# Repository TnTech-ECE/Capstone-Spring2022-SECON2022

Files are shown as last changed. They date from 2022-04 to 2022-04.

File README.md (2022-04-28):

# SECON2022
## Tennessee Tech SoutheastCon 2022 Robot Project
## Executive Summary
The goal of this project was to design and build an autonomous robot to compete in the 2022 IEEE SoutheastCon Student Hardware Competition. 
The theme of the competition was Mardi Gras, and the competition format reflected this. The robot had to navigate a track while completing 
tasks and avoiding obstacles, all within a three-minute time limit. The team consists of two Electrical Engineers and two Computer Engineers. 
The engineers on this team leveraged their academic background in microcontrollers, power, and control systems, and acquired other necessary 
knowledge in areas such as computer vision and Mechanical Engineering. 

## Version Contained In This Repo
The version of the project contained in this repo has been updated since the competition. All software files necessary to play the full game 
are contained under the Software heading.

## Outcomes
Due to last minute optimizations before the competition, the team was unable to showcase the full design and capabilities of the robot. 
This project earned a ranking of 7th place out of the 38 teams that attended the competition. The initial proposed budget for this project 
was $2000, and the final BOM indicated a final budget of $2,023.49.

## Video

<figure class="video_container">
  <iframe src="https://youtu.be/yNQZh_yY1AQ"> </iframe>
</figure>

## Pictures
### Front of Robot

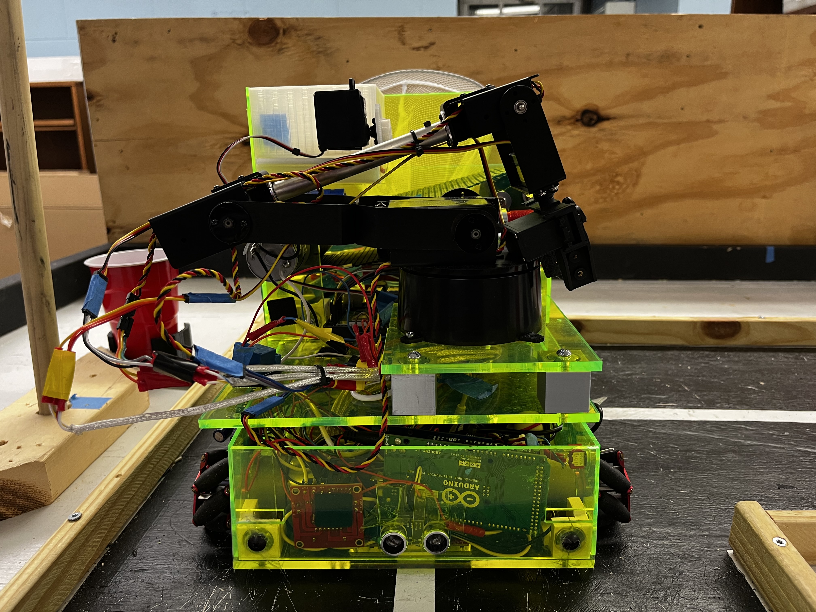
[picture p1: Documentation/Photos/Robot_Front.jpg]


### Right Side of Robot

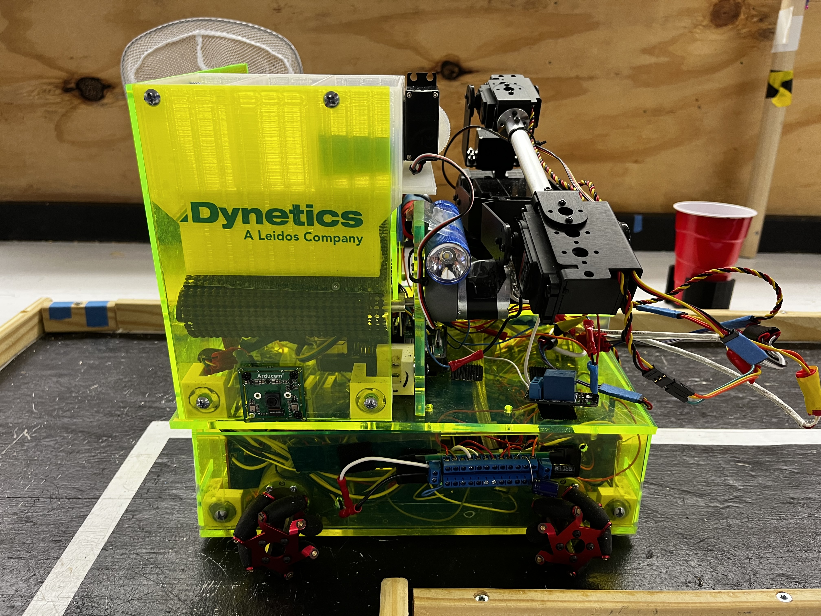
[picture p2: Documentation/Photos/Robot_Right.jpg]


### Left Side of Robot

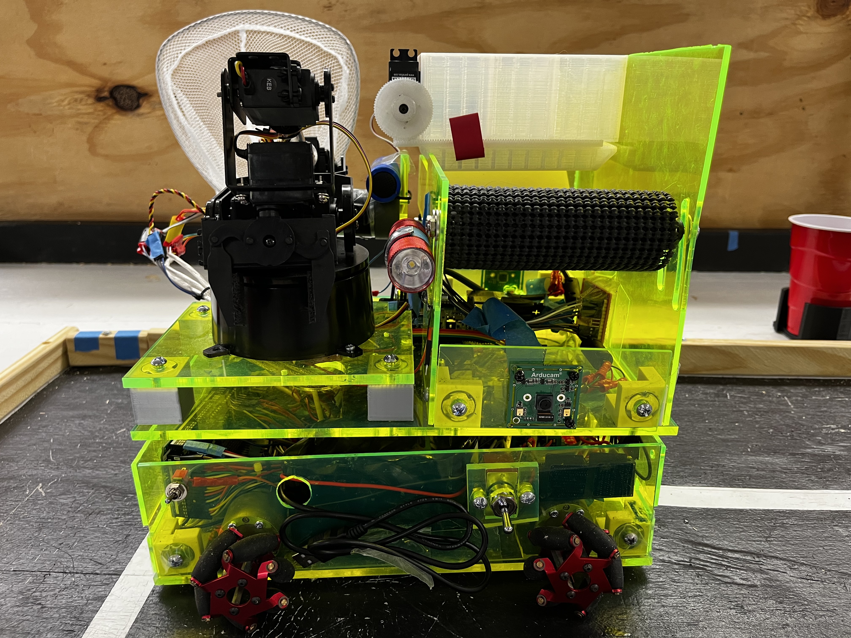
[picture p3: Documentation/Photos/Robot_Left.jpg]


### Back of Robot

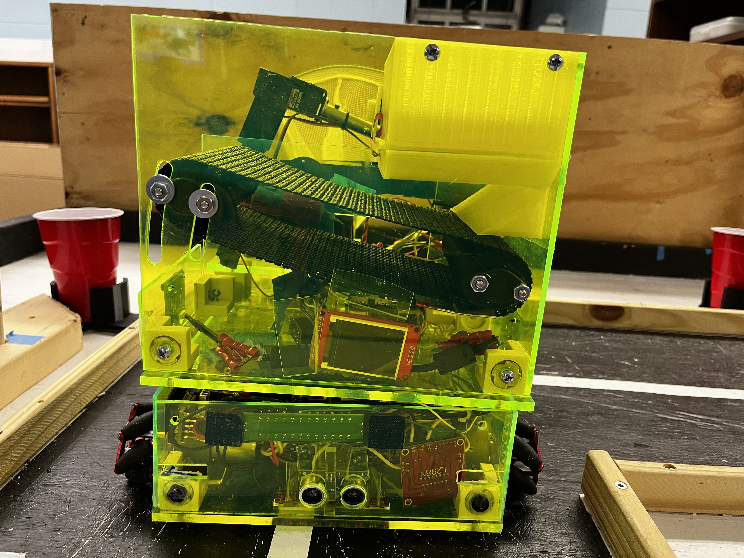
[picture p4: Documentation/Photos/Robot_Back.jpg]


### Top View of Robot

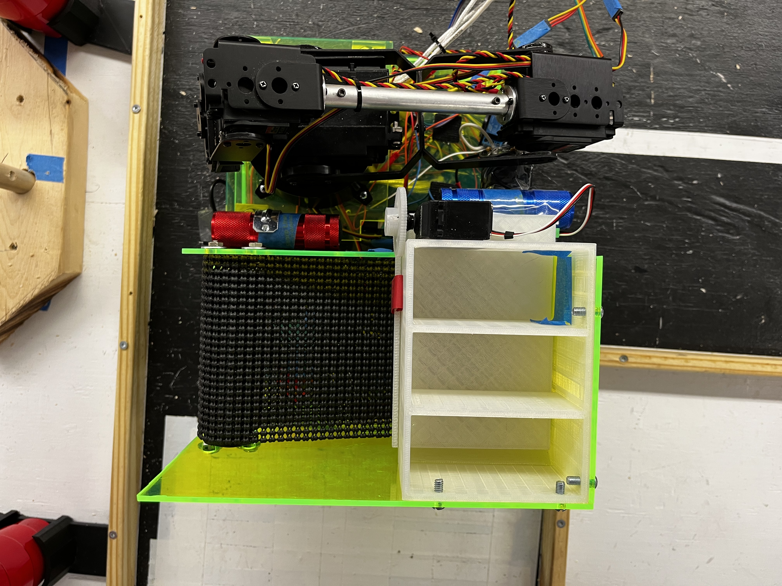
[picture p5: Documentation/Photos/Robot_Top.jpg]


### Interior of Lower Chassis

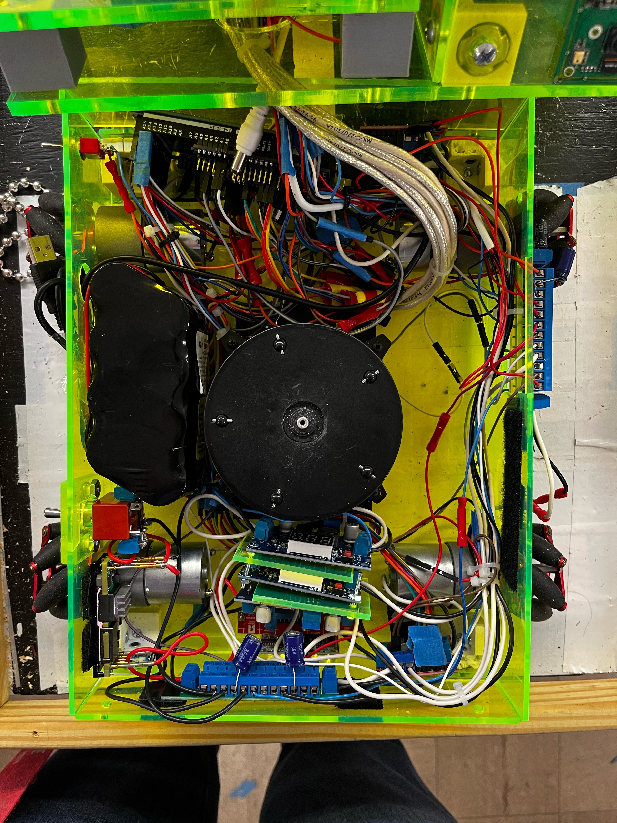
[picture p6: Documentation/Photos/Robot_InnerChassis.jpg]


## About Us
As mentioned in the summary, this team consisted of two Electrical Engineers and two Computer Engineers. The two Electrical Engineers are 
Chase Garner and Sawyer Hall, and the two Computer Engineers are Daniel Summers and Lexi Sheeler. The faculty member that oversaw the 
development of this project is Jesse Roberts. There was no customer for this project, however the project was designed to meet the 
specifications provided by the competition organizers.

## Repo Index
### Project Documentation
<ul>
  <li>Design Documents
    <ul>
      <li>3D Models</li>
      <li>Power</li>
    </ul>
  </li>
  <li>Bill of Materials</li>
  <li>Datasheet</li>
  <li>Project Poster</li>
  <li>Photos</li>
</ul>

### Reports
<ul>
  <li>Project Proposal</li>
  <li>Design Phase 1</li>
  <li>Design Phase 2</li>
  <li>Final Report</li>
</ul>

### Software
<ul>
  <li>Raspberry Pi</li>
  <li>SECON_Arduino</li>
</ul>

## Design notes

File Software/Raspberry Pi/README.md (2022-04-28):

## File(s): 				
detect_shapes.py, shapedetector.py, colorlabeler.py, shapeLength.py

## Author(s): 				
Daniel Summers, Lexi Sheeler

## Target Hardware: 		
Raspberry Pi 4 (4 GB) Running Ubuntu 21.10

## Purpose: 				
 This software is responsible for the Vision System of Tennessee Tech's SoutheastCon 2022 Robot. This software will detect the presence
						of nets on the game board and communicate this to an Arduino MEGA 2560 over serial communication. Additionally, this software will output
						an image to a TFT Screen. This serves as a method of achieving points as well as indicating that the Pi is running correctly.

## Software Dependencies:	
Python 3 (Necessary Libraries: imutils, cv2, serial, digitalio, board, PIL, adafruit_rgb_display), the file Tech.bmp (this is the bitmap
						image to be displayed on the TFT screen)

## External Connections:	
This software is designed to be ran in conjunction with an Arduino MEGA 2560 (see SECON2022/Software/SECON_Arduino for software) via UART.
						Reference SECON2022/Documentation/DesignDocuments for all external hardware connections. 
						
## Installation:			
Download and Install Python3 and its necessary libraries to the Raspberry Pi using apt and PIP (each where necessary)

## Running/Use:			
These files are designed to be ran with sudo priviledges automatically on boot up. To accomplish this, the default user of the Pi must be 
						given the necessary sudo priviledges, and the console command 'sudo python3 detect_shapes.py' must be added to the list of commands to be ran
						on startup. The team implemented this by adding the command to the default user's .profile script (Note: for this workaround, requiring the 
						default user's password when executing sudo commands must be disabled. This is a security risk that should not be implemented if the Pi is to
						be used for other applications.)

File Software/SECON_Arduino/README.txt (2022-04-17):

File: 					SECON_Arduino

Author(s): 				Chase Garner, Sawyer Hall, Daniel Summers

Target Hardware: 		Arduino MEGA 2560 with Adafruit Servo Shield

Purpose: 				This software is responsible for the motor control and sensor readings for Tennessee Tech's SoutheastCon 2022 Robot. 
						This serves as the main gameplay control for the robot.

Software Dependencies:	Ardunio IDE

External Connections:	This software is designed to be ran in conjunction with a Raspberry Pi (see SECON2022/Software/RaspberryPi for software) via UART.
						Reference SECON2022/Documentation/DesignDocuments for all external hardware connections. 
						
Installation:			Connect the Arduino MEGA 2560 to a computer via USB. Using the Arduino IDE, flash the given code to the Ardunio.

Running/Use:			After installation, the code will automatically begin running when the Arduino is powered on. Immediately after powering on, the 
						robot will begin calibrating. At this time, the line following sensors (See SECON2022/Documentation/) should be calibrated by providing
						them with a reference for both black and white (This implementation expects a white line with a black background). After calibrating,
						the arduino will entire a standby loop until the start switch is flipped (the GPIO input pin connected to the start switch will have its
						pull up resistor enabled, driving its signal high. Connecting the other side of the switch to Ground will pull the GPIO pin down when the 
						switch is flipped, starting the gameplay routine. Any input of 0/Ground on this pin will achieve the same result. Power Cycling the robot 
						is required to restart the routine.

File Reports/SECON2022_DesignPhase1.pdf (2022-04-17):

# Design Phase One

Chase Garner, Sawyer Hall, Lexi Sheeler, Daniel Summers
Electrical and Computer Engineering Department Tennessee Technological University Cookeville, TN
ncgarner42@tntech.edu, sjhall43@tntech.edu, aasheeler42@tntech.edu, dbsummers42@tntech.edu
I. INTRODUCTION
A. Problem Definition

The South Eastern Conference (SECon) is a yearly IEEE event comprised of several competitions. One such competition is the hardware competition, where students from many schools across the region design and build a robot to compete in a unique challenge. Because the conference is being held in Mobile, Alabama, the competition is Mardi Gras themed to reflect the history and origin of the festival. This year’s hardware competition requires the robot to navigate an L-shaped street within a three-minute time limit. In addition to navigation, the robot can complete challenges to earn points. The tasks include: removing beads from a “tree”, placing the beads in “trash bins” or shooting them into fishnets, and moving a marshmallow off the roadway into gaps in a barricade.
There are several rules and specifications that the design must adhere to. The first and potentially most important constraint to meet is that the robot requires complete autonomy. To meet this constraint, the robot must be capable of decisionmaking to identify randomly placed obstacles and challenges. In addition, the robot must be contained within one cubic foot at the start of the competition, but may expand beyond this specification after the run has started. It is also specified that the robot may not break apart and must remain one unit for the entirety of the run. Finally, the robot may not cause damage to the track or harm bystanders. Any violation of these constraints will result in immediate disqualification at the judges’ discretion.
B. Conceptual Design

At the beginning of the design process, key competition rules and point gaining tasks were identified. The point breakdown played into the first design phase in several ways. The scoring scheme was broken down and the maximum number of achievable points was determined. This allowed for selecting which way the robot could earn maximal points without the need to complete every task outlined in the guidelines. This led to a design that is targeted towards shooting beads into the nets instead of trying to place them into the cups along the sidewalk area. Along with this decision, the team also elected to not place high importance on removing the marshmallow from the track because it is only a one-point deduction if left on the track. No attainable designs were identified by the team, and focus was instead placed on areas which are integral to being competitive, such as the navigation system and drive train.
The robot is broken down into seven systems: main controller, power, navigation, drive train, appendages, shooting mechanism, and peripherals. Each system is then broken down further into atomic subsystems. There will be three microcontrollers: the main controller, a navigation controller, and a peripheral controller. Serial communication will be used between the main and navigation controllers, and the peripheral controller will only require power to operate. The main controller is responsible for interconnects between systems, excluding power, which will directly connect with all systems. For the next phase of the design process, component specifications will be defined first at an atomic level, then working up until the whole system has been defined.
C. Broader Impacts

Beyond the competition itself, this project aims to serve as a way to demonstrate the quality of both the Tennessee Tech Electrical and Computer Engineering (ECE) Department and the Tennessee Tech IEEE. The Tennessee Tech IEEE chapter has a longstanding tradition of fielding competitive, winning teams at SECon, and this project serves to continue such a tradition. Additionally, due to the current pandemic, interest and involvement in the IEEE chapter has massively decreased over the last two years. This project will generate more interest in IEEE from ECE students while also providing IEEE members with hands-on experience with robotics and programming. Because of the involvement of the IEEE chapter, the design of the peripheral system was changed to use its own microcontroller and an analog circuit to control the LEDs. This allows the IEEE members to work on these systems independently of the robot’s development, and it ensures they receive experience in elements of both electrical and computer engineering by incorporating both analog and digital circuitry and programming.

D. Larger Process

The Design Phase I document is written with the intent of removing ambiguity and presenting a more clearly defined system. The document should leave the reader with a clearer understanding of how the competition has led the team to make the design choices presented in the following sections.

In addition, ideas presented in this document will be further built upon in future design phases.

II. CHASSIS

The robot’s chassis will be divided into a lower section, which will house the majority of the electronics, and an upper section, which will serve as a platform for the robotic arm and shooting mechanism. The chassis and all external systems must conform to the 1 cubic foot constraint set by the competition. Because of its size and simple structure, it is intended for the chassis to be constructed with acrylic sheets instead of 3D printing it, but additional material options are still being considered. The main justification for this decision is the team’s desire to avoid possible 3D printer errors that are likely to occur during the longer print times that would be necessary for the larger aspects of the chassis. In order to verify that the chassis conforms to the 1 cubic foot limit while still maintaining enough volume to house the robot’s internal components, the chassis will need to be a somewhat detailed 3D model. Additionally, the size of the robot should be minimized in order to allow for a smaller turning radius. The lower chassis (Figure 1) will be a stationary platform in order to minimize the amount of turning required. With a 1 square foot footprint, the robot would be over 16 inches diagonally. This could prevent the robot from turning within the 16-inch width of the track. Instead, the lower chassis will only be required to turn during the two 90 degree turns in the track, where the effective width is much wider. The lower chassis will contain the drivetrain, navigation sensors, each of the microcontrollers, and the power supply circuitry, including the battery. The main purpose of the lower chassis will be to house these components, but it will also be responsible for collecting the marshmallow obstacle from the track. It is the intention of the team that collecting and pushing the marshmallow will be handled by a passive system that will be incorporated in the chassis’ shape and design, but the exact specifications of such a passive system must still be determined. The main constraint of the lower chassis will be the size limitation of the competition. The chassis, including the wheels on each side and the passive marshmallow system on the front, must all fit within the 1 square foot footprint of the robot.
Instead of requiring the entire robot to turn and face each target, the upper half of the chassis will be constructed in such a way that it will freely rotate at least 180 degrees to allow for the shooting mechanism to “aim” in each direction. However, the rotation must not interfere with the wiring connections between the lower and upper chassis. This turntable will house the robotic arm and the shooting apparatus. Additionally, the upper chassis (Figure 3) will serve as a storage mechanism for the beads between being collected and being shot into the nets (Figure 2). Upon being placed into the storage mechanism, the beads must be sorted into three separate containers to be individually loaded into the shooting apparatus. The number of containers was chosen in order to comply with the competition rules stating that additional points would be awarded for each

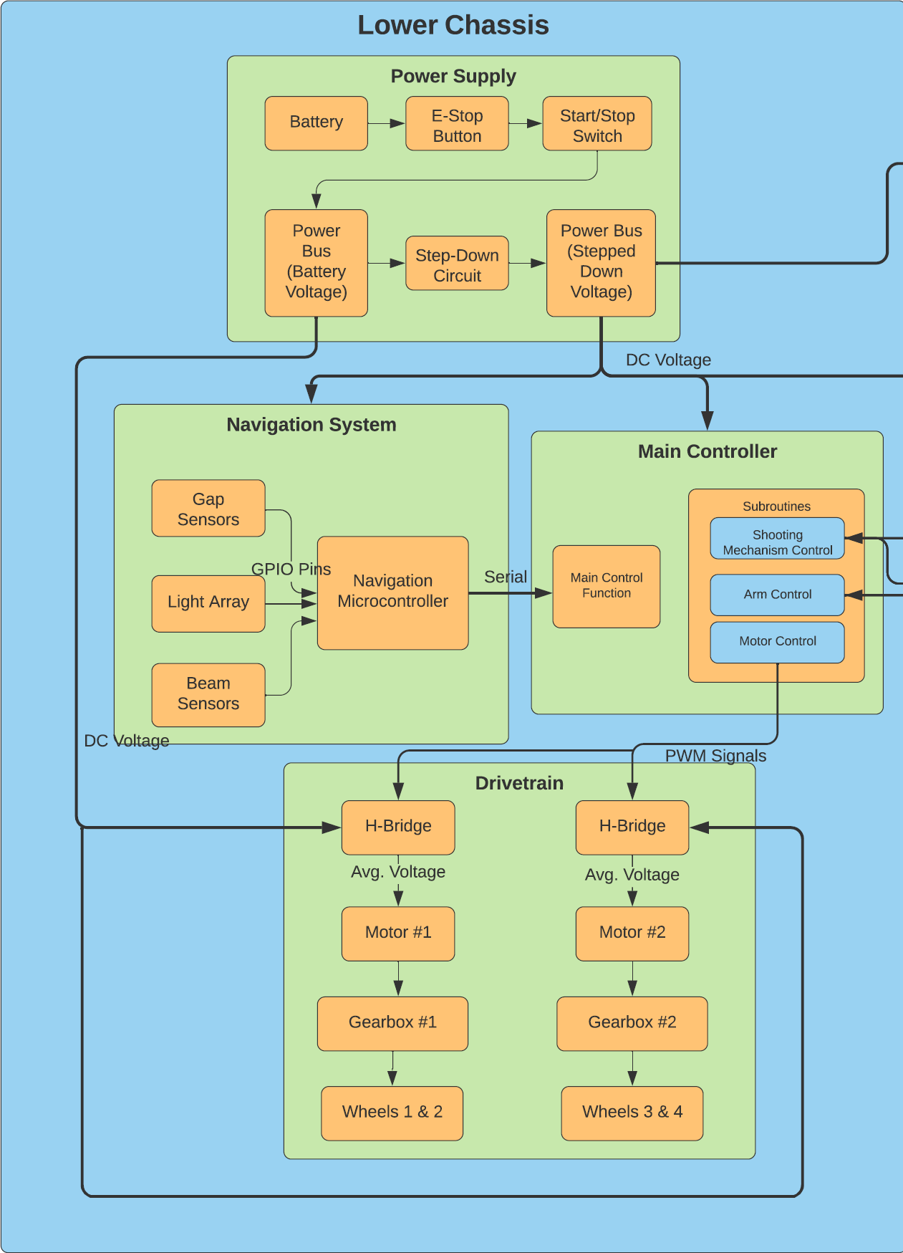
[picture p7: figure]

Fig. 1. Lower chassis block diagram

net containing at least one bead. Because there are three nets, three was chosen for the number of containers. These containers will be bottomless, but the housing of the shooting mechanism will serve as a temporary bottom. To “reload”, the containers will be moved over an opening in the housing, allowing the beads to fall onto the belt. However, this method must be tested to ensure that the beads consistently do not get stuck in the sorting mechanism. In order to test the most optimal sorting configuration, a physical mock-up of the system must be constructed. The dimensions of the divider will then be experimentally varied and the percentage of beads in each container, as well as the percentage of beads that get stuck, will be measured. The configuration that yields the most balanced percentage of sorted beads and the lowest percentage of stuck beads will be chosen for the final design.

III. CENTRAL CONTROLLER
The central controller (Figure 4) of the robot will consist of a single Arduino Mega 2560 microcontroller. This specific hardware component was chosen for its robust functionality, simple programmability via Arduino’s predefined libraries, and large number (54) of General-Purpose Input-Output (GPIO) pins, of which 15 can be used to generate Pulse Width

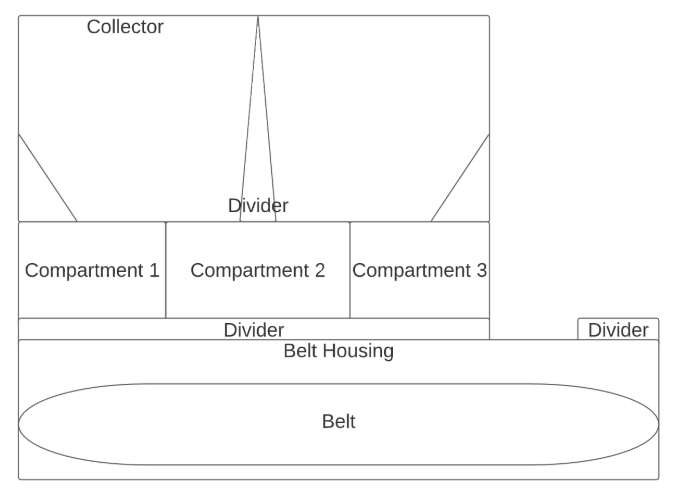
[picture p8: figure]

Fig. 2. Loading mechanism

Modulation (PWM) signals. The microprocessor operates at 5 Volts and is recommended to be powered by 7-12 volts which will be provided by the step-down circuitry of the robot’s power supply [1]. Additionally, a serial connection must be established between the central controller and the navigation system. This serial connection will relay commands from the navigation system’s microcontroller to the central controller, where they will be interpreted in order to determine the proper control subroutines to be run. This interpretation and serial communication will be handled by the central controller’s main control function, which will then trigger a number of separate subroutines that are responsible for the central controller’s outbound communication to the motors, arm, and shooting mechanism.
The motor subroutines will communicate with the drivetrain’s motor drivers via its GPIO pins to achieve the desired speed and direction of each of the two motors. This functionality will include both starting and stopping the motion of the robot, navigating the 90 degree turns in each direction, and propelling the robot both forward and backwards along the track. The arm subroutines will function by using inverse kinematics to provide the necessary positional information to each of the arm’s servo motors to achieve the desired endpoint position of the arm. Such routines will include picking the beads from each tree and placing the beads in the chassis’ storage container. This information will be provided to each individual servo via dedicated GPIO pins. Lastly, the subroutines related to the shooting mechanism will be responsible for rotating the upper platform of the chassis to “aim” the mechanism in the correct direction, providing a signal to the shooting belt’s motor, and ”reloading” the mechanism by shifting the storage container to allow for the next set of beads to fall onto the belt. Each of these motor control subroutines will drive separate PWM pins of the central controller. Consequently, each of these subroutines will accept additional feedback inputs from these external systems. This feedback will be used to align the subroutine’s expected

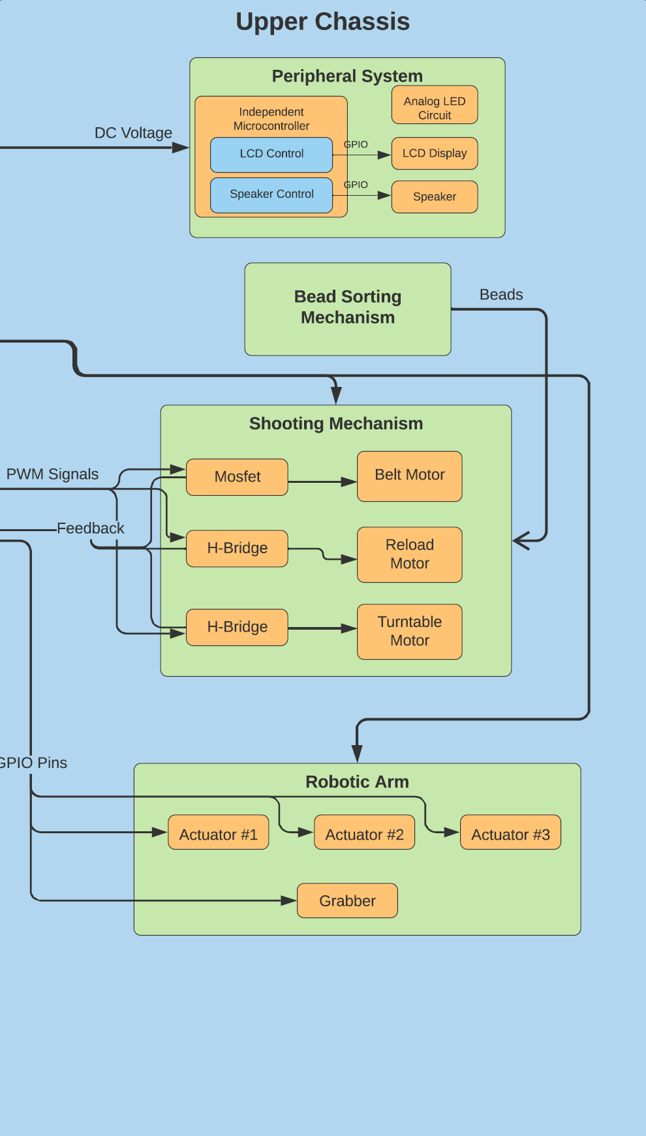
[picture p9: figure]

Fig. 3. Upper chassis block diagram

behavior with the actual behavior of the mechanical parts and will be provided via additional GPIO pins.
Because of the software-based nature of the central controller, the elements of the programming language can be assumed to behave in the way they are defined by the language. However, the software’s behavior must be closely emulated when simulating and testing the various components driven by the software. Without closely representing the software during this testing, the components under test can not be guaranteed to behave in the same manner when they are controlled by the software. In addition, extensive experimental testing will be required to adjust the software to meet specific needs of the robot. For instance, timing tests must be conducted to ensure that enough time has passed for all of the beads to be launched by the shooting mechanism before the motors are turned off.

Lastly, the datasheet of the Arduino must be thoroughly read and understood to ensure that the microcontroller is capable of producing the output voltages and currents required by the component hardware.

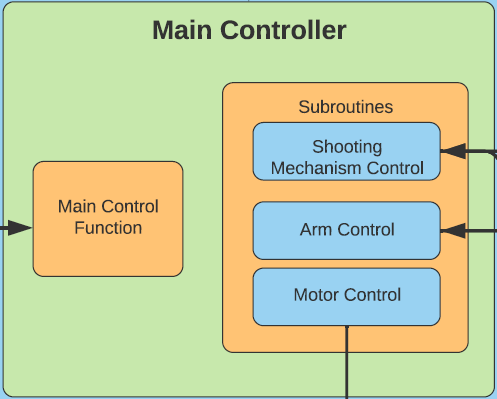
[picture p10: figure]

Fig. 4. Central controller block diagram

IV. POWER

The battery voltage will be determined by what is needed to power the DC motors. Because of competition specifications, the robot is required to have a visible and easily accessible emergency-stop. To ensure no damage to components, the emergency stop is intended to stop only moving parts of the robot. Therefore, the emergency-stop will be the interim between the battery and motors. The emergency stop will be utilized to stop the robot in case of a major malfunction. Like the emergency stop, the competition specifications require the robot to have a clear start/stop switch. The start/stop switch will then be connected from the emergency stop to the power bus. The power bus will distribute the primary voltage to the step-down circuit and the H-bridge. The H-bridge will then connect the needed voltage to the DC motors. The step-down circuit will then decrease the battery voltage to the needed voltages for the rest of the components. The step-down circuit will be purchased and not built by the team. The step-down circuit will then be connected to two separate power buses. The peripherals will be connected to one power bus, while the navigation sensors and main controller will be connected to the other. The power circuit will need to be tested through the utilization of LTSpice. The team will test the step-down circuit and will then know that the systems work correctly by finding the output voltage and current at the step-down circuit.

V. NAVIGATION

The navigation system (Figure 6) is responsible for identifying objects and making decisions based on inputs from a light array, beam sensors, and gap sensors. These decisions will

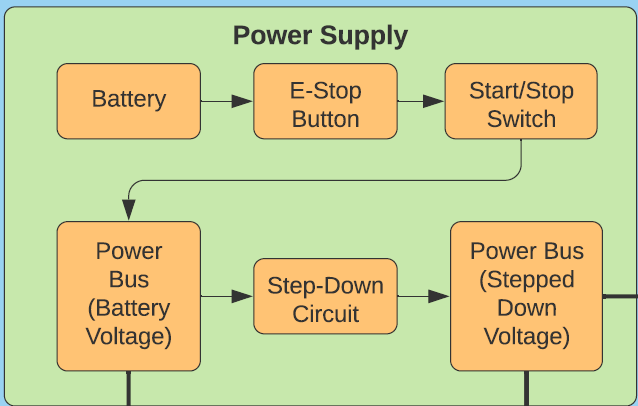
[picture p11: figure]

Fig. 5. Power system block diagram

then be sent to the main microcontroller via serial communication and relayed to the necessary systems. All transmissions between these microcontrollers will include an acknowledge message when the receiving controller accepts the instruction message.
Due to high computational demand and number of available ports, it was decided that the navigation system should include its own microcontroller as to not overwhelm the main controller. The navigation system will require constant monitoring of the sensors, as well as decision making based on the inputs, making this a completely separate system, except for serial communication with the main microcontroller.
The navigation microcontroller will enable interrupts from sensors after the turn around at the end of the track. If the sensor detects specific objects, it will interrupt the drive commands and prompt the correct subroutine. This information will be sent to the main microcontroller in a series of commands: adjust left, adjust right, forward, backward, left turn (90°), right turn (90°), ready to shoot, and arm ready for pick-up/drop. These commands will be appropriately carried out by the main microcontroller and other necessary systems. The light array will be mounted on the underside of the base to assist with track traversal, using the painted white line on the track. The array will allow for small deviation from the painted white line, but will trigger left and right adjustment commands to be sent to the main microcontroller if it strays too much. If the sensor detects a 90° angle in the line, it will send a corresponding command to turn in the correct direction. When it reaches the end of the line, it will send a message to reverse.
The beam sensors will be used to differentiate between power poles and nets based on height. There will be two beam sensors mounted on each side of the chassis, one at approximately 5” and the other pointing up aiming for approximately 18”. When both sensors on one side detect an object, it is identified as a power pole and the robot will continue moving. If only the lower sensor detects an object, the obstacle will be labeled as a net, and a message will be sent from the navigation system to the main microcontroller.

The main microcontroller will follow instructions directing the robot forward or backward until the shooting mechanism is properly lined up. When the mechanism is lined up, the navigation system will then send a ready to shoot command to the main microcontroller to allow the shooting mechanism to fire. After fired, the navigation system will proceed forward and repeat the process until all three nets are identified and beads are fired. At this point, the robot will return to the starting square and end the round.
The gap sensors will also be mounted on the side of the chassis and identify 4” gaps in the barricades. When a gap is identified, the navigation system will alert the main microcontroller which will then trigger the marshmallow subroutine to move the marshmallow off the roadway through the gap. While conceptually these sensors should work, issues may arise further down the line. Options for individual sensors and the overall system are continually being researched to find the best fit. After researching what sensors would be best, the team decided on the beam sensor for identifying nets, but are unsure of what complications may arise in testing relating to the netting material. Because the material is thin and not solid, most sensors will be unable to detect it, which is why discernment is taking place by pole height.
Due to the nature of the system, it will be primarily software, which is difficult to analytically test and measure. As long as used properly, predefined library functions will operate as expected, so the majority of testing will take place on communication between the microcontrollers. For testing purposes, signals sent from the navigation system will be measured and compared to signals received by the main microcontroller.

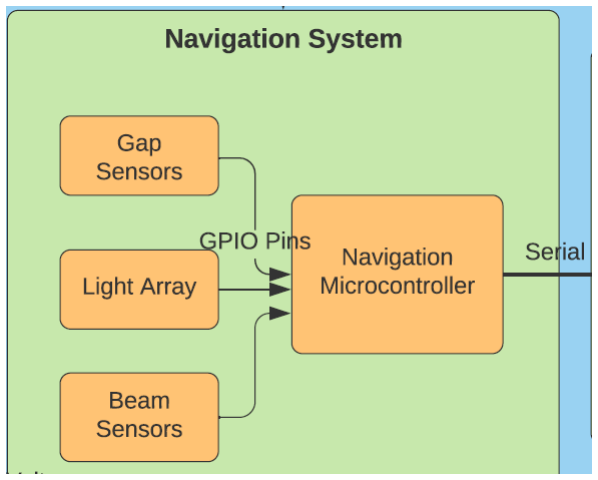
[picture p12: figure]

Fig. 6. Navigation block diagram

VI. DRIVE TRAIN
This year, the environment that the robot will compete in is an L-shaped track. A large portion of the available points in the competition are rewarded solely based on the robot being able to navigate the track back and forth. As such, robot mobility is a critical component of the competition, and vital for the team’s success.
The drivetrain subsystem of the robot (Figure 8) is responsible for moving the robot along the track. “Drivetrain” is an umbrella term that includes all parts that enable the robot to move through space, e.g., motors, wheels, gears, and so on. The drivetrain of this robot will be designed as a differential drive. A differential drive operates on the concept of moving the wheels at different speeds to enable steering. In total, the robot will have two DC motors and four wheels. The pair of wheels on either side of the robot will be connected to their respective motors via a system of gears, belts, or combination of both. One specification that the team will have to keep in mind is the size spec of the robot. The robot will need to be contained within 1 cubic foot which means that the drive train can be at most 1 square foot in area.
Selecting the right motor and understanding its performance characteristics is an important part of designing a drivetrain. A generic graph of DC motor performance is shown in Figure 7.

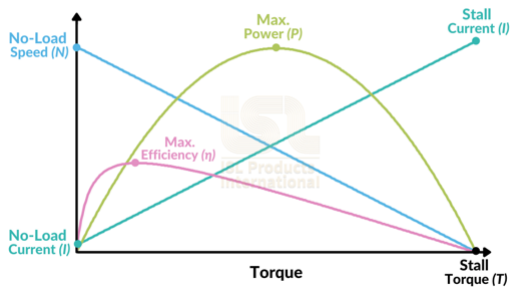
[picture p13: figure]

Fig. 7. Calculations of Arm

As can be seen in the figure, speed and torque of a motor are inversely proportional. As torque increases, speed gradually decreases. In addition, current and torque are directly proportional. At very fast speeds, the motor consumes little current and produces very little torque. This is an issue that can be alleviated with the use of gears. Attaching a gearset to the motor shaft will cause it to run at a lower speed, thus consuming more current and generating more torque. The amount of torque needed in this application is dependent on the weight of the robot and the desired acceleration. Given that the competition environment is a level track, it is not expected that a great amount of torque is needed. Only enough torque is needed such that the robot can accelerate at a reasonable rate and then maintain its velocity. For these reasons, it was decided that two DC motors would suffice. Using only two motors to drive the robot decreases the amount of complexity and needed parts when compared to driving four motors separately. In addition, the team will need to determine how fast the maximum speed of the robot should be when navigating the track, and from there determine the gear ratio necessary to accomplish the task. Gear ratios work to linearly decrease the speed of the motor shaft. For example, a gear ratio of 2:1 means that the shaft will spin twice as slow and generate twice as much torque. Many DC motors come with predetermined gearboxes already attached to the shaft and are referred to as geared motors. Geared motors are a common solution in mobile robotics applications.
As the robot must be completely autonomous, this means that no member of the team will be allowed to do anything to affect the robot’s performance after the run has started. Autonomous operation of the robot will require that the drivetrain system receives commands from the main microcontroller that detail speed and direction for the motors. The method of motor control will have to utilize feedback so that the commanded velocities are not random and reflect where the robot needs to go. One very common method of control is the Proportion, Integral, Derivative (PID) loop. This method of control is common in navigation applications. The proportion coefficient corresponds to how large the error is at any given time, the integral coefficient corresponds to the duration of the error, and the derivative coefficient corresponds to how quickly the error is changing. Using a combination of the three will allow the robot to navigate autonomously while maintaining the desired course.
PID controllers are only effective when they have been properly tuned and utilize the optimal coefficients. Methods of tuning a PID controller vary depending on the system in question. For an autonomous robotic application, a model-based approach may be appropriate. The electrical characteristics of DC motors are well understood, and they can essentially be modeled as a series RL load. This is advantageous for the engineers because a good starting point can be found even without hardware. One software that can be utilized to create a simulation is Simulink. In Simulink, the team would be able to create models of the system and test the responses. Graphs of the response can be created in Simulink that give a visual representation of the system response to error. One thing to consider when viewing these graphs is how much power is required to achieve the response. The amount of power will need to be feasible for our system. Any model-based tuning of the system would of course have to be manually tested by entering the determined PID coefficients into the motor controller and testing the navigation capabilities of the hardware itself. Once the coefficients have been entered into the hardware and the navigation performance has been tested, further tuning will likely be required in order to optimize the performance of the system. This will consist of changing each of the coefficients independently to see how it affects the system. The team will need to have a good understanding of how each coefficient affects the system so that this process relies less on trial and error. It is desirable that the system have a quick yet smooth response to error and that it is able to navigate the entire track while following the white line in the center.

The motor controller will generate Pulse-Width Modulation (PWM) signals to either a dual-motor H-bridge unit or two separate H-bridges that will provide power to the motors. PWM is a method of rapidly opening and closing a switch in a circuit that contains some main power source. The act of opening and closing the switch gives the engineer control over the output voltage to the load. A higher duty cycle (the percentage of the time the switch is closed) will result in a higher average voltage, and vice versa. PWM is advantageous to this project because it will allow the robot to spin wheels on either side of the unit at different speeds, giving the robot the ability to turn and navigate more easily. The team will need to determine a top speed for when the error is zero and the robot is driving directly along the line. All other commanded speeds will be calculated as a percentage of the top speed using the error and PID coefficients. The method of verification for the motor drivers will be LTSpice. An H-bridge is modelled as four transistors, two on each side of the motor. The direction of the current through the motor can be changed by biasing the different transistors, which in turn changes the direction of the motor. The PWM signals from the microcontroller will need to be simulated to ensure that they drive the H-bridges to give the correct average voltage to the motors. Once hardware is obtained, the team will use lab equipment such as the DMM to ensure that the voltage requirement is met.

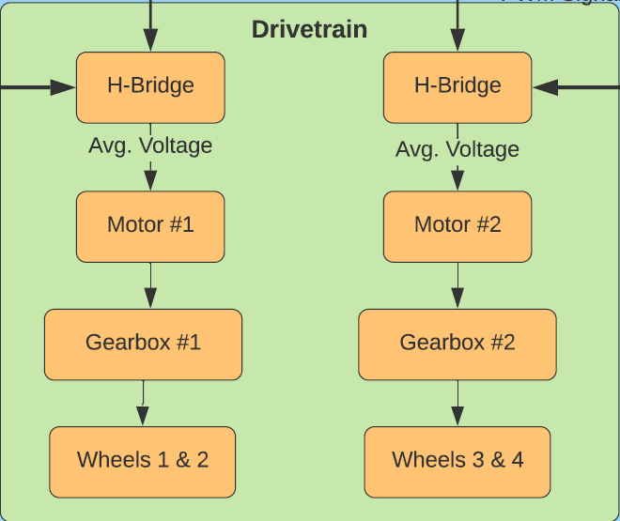
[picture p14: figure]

Fig. 8. Drivetrain block diagram

VII. SHOOTING MECHANISM
The shooting mechanism (Figure 9) is a critical subsystem because of how the team has decided to maximize the number of points achieved. The shooting mechanism will allow for beads to be launched into vertical nets. This mechanism will be placed on the upper chassis, enabling it to shoot in either direction. The mechanism itself will consist of a belt and one motor, placed below the storage container on the chassis. When the main controller receives the shoot command from the navigation system, it will enable the belt motor. At this point, the beads will be dropped onto the belt and accelerated to the speed required to reach the nets.
Prior to physical testing, modeling software will be used to test angle, velocity, and distance. Mathematical methods, such as projectile motion equations, will also be used for testing purposes. The team will need to ensure there is enough friction and speed on the belt for the beads to be appropriately launched. Belts with different materials and topologies will need to be tested.

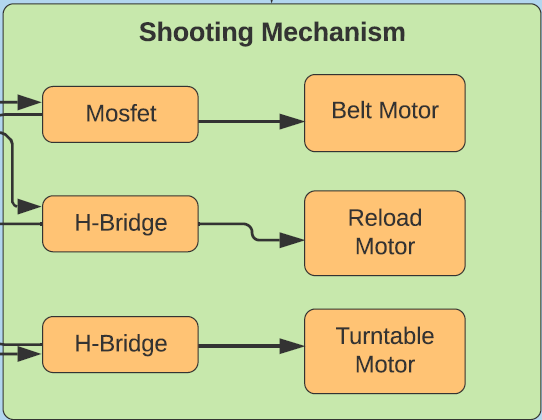
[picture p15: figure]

Fig. 9. Shooting mechanism block diagram

VIII. ARM

The robot arm (Figure 12) will receive power from the battery and inputs from the microcontroller. The microcontroller will send signals to servos 1-3 to position the robotic arm. Using the practice track, the arm will be preprogrammed to remove the beads from the trees. Once grabbed, the robotic arm will then receive a subroutine command to move the arm to the position to drop the bead/beads into the container to be shot. After this, the microcontroller will then command the servos to move to a home position. The robotic arm will be utilized again once the robot reaches the end of the track. The robotic arm design will need to be tested in many different aspects. For one, the feedback and functionality of the servos will need to be tested using Simulink. The team will also have to use analytical testing to find out the needed lengths of each section. The team will need to know the reach achieved by each section of the arm, which will then be added together to find out the end total reach achieved from the extended arms. The length of each section of the arm will be determined by the desired height and reach of the arm (Figure 10).
The team will also need to consider the grabbing mechanism length to add to the total distance achieved. The gameplay rules outline the specifications for the track [2]. The drawing can be seen in Figure 11. From the drawing, the team can see that there is a height window from the top of the branch

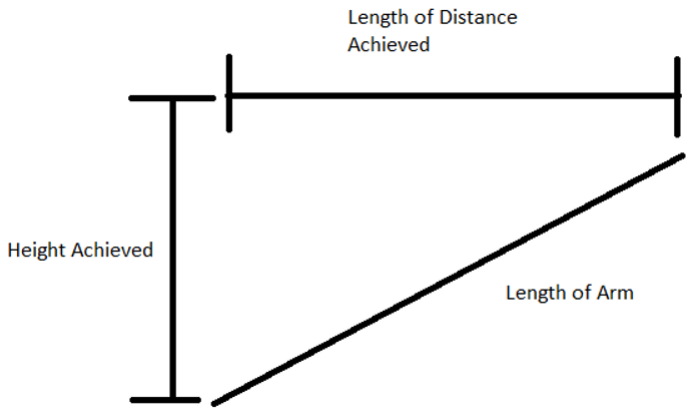
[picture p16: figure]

Fig. 10. Calculations of Arm

and to the bottom of the hanging beads of 6”- 9” from the top of the robot. The team can also see that there is a length window from the front of the branch to the back of the branch ranging 6” - 12” from the side of the robot. The combination of the analysis plus the gameplay rules outline will determine the lengths of the arms.

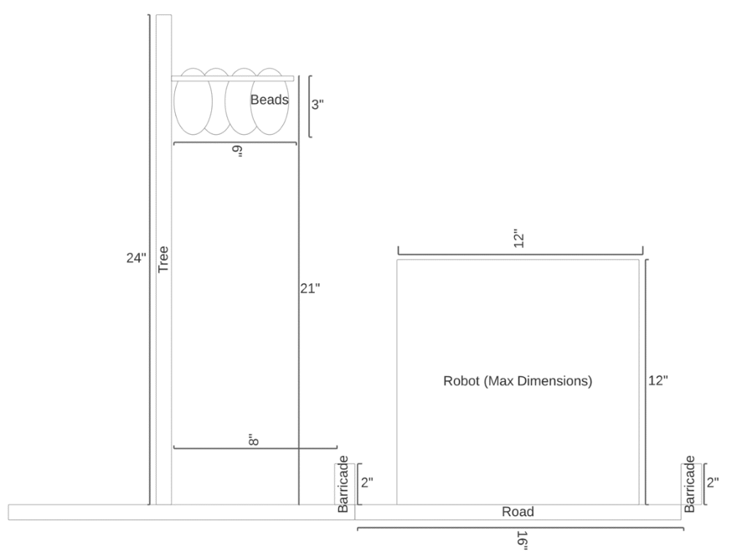
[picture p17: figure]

Fig. 11. Gameboard specifications

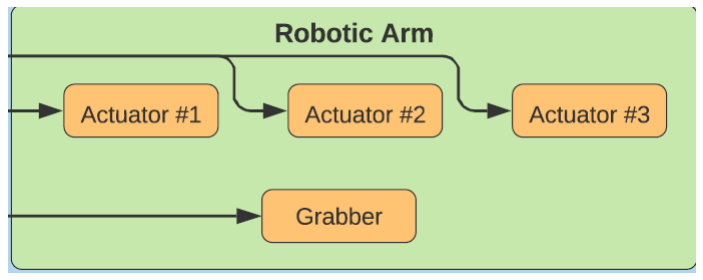
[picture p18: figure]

Fig. 12. Arm block diagram

IX. PERIPHERALS

The peripheral system (Figure 13) is responsible for controlling the visual and aesthetic elements of the robot in order to receive the maximum number of competition points. Because of the non-critical nature of such a system, the peripherals will not communicate or receive any inputs from the other subsystems except for a constant voltage from the power supply system. Furthermore, this system will be broken into two distinct elements. The first element will be an analog circuit responsible for lighting the various LEDs that will decorate the robot. This will be a simple circuit that connects the LEDs to the power supply and pull-down resistors. The second element of the peripheral system will be a small microcontroller responsible for powering and controlling both the LCD display and a speaker via separate functions. For the LCD display, the function will be responsible for displaying a hard-coded image/set of images and text, and for the speaker, a preselected song will be played using either the microcontroller’s GPIO or DAC pins.
In order to verify the operation of the peripheral system, an LTSpice simulation of the analog LED circuitry will be required. This analysis will be used to determine the ideal number and configuration of the LEDs, as well as the ideal component values of the elements of the circuit that will make the LEDs flash or blink. Additionally, if the DAC of the microcontroller is to be used for the speaker, further LTSpice testing must be conducted to test whatever amplification circuitry, if any, that will exist between the DAC and the speaker itself. Lastly, the output signals of the microcontroller must be experimentally verified to ensure that the correct waveforms are being generated before they are sent to the external hardware.

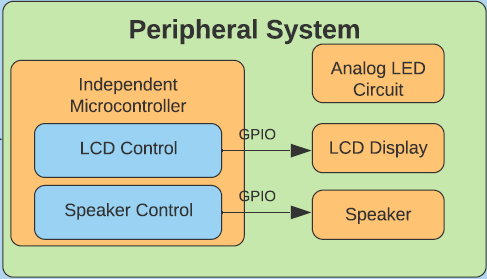
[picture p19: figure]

Fig. 13. Peripherals block diagram

X. ARCHITECTURAL RISK ANALYSIS

It is also vital to consider the inherent cybersecurity risks associated with any proposed design. This Architectural Risk Analysis (ARA) is critical in order to develop a solution that considers and mitigates the possible threats and vulnerabilities of the system. The nature of this design’s purpose presents a unique angle from which risks must be assessed and addressed.

Both the nature and rules of the competition apply a heavy influence on the overall ARA of the design.
Because of the nature of the competition, it is expected that other contestants will make attempts to attack and impede the design. The most likely attack scenario will involve the variety of sensors on the exterior of the robot. The communication between the sensors and the microcontrollers will be contained within the confines of the robot itself and will not utilize any wireless communication. Therefore, the most likely method of attack will be directed at the measurements taken by the sensors themselves. For example, a bright light could be used to disrupt the infrared sensors and cameras. In order to mitigate such risks, extensive experimental testing in a variety of environments and conditions must be conducted prior to the competition to determine the risk of such attacks and to properly adjust the sensors to be more resilient to nonideal conditions.
While the competition presents a higher chance of attack, one of its most critical aspects also minimizes or eliminates the majority of the design’s attack surface. The competition rules state that the robot must be completely autonomous and that team members must verify this by suspending any outbound communication from any personal devices (laptops, cell phones, etc.). Because of this stipulation, the overall attack surface is minimized by design. Since no inbound communication is expected by the robot, there are also no vectors for attackers to utilize to penetrate the system. The robot will function as a fully isolated system, so no opportunities for attack will present themselves by design. Also, it is safe to assume that outbound communication from competitors’ devices will also be restricted, as they are also actively competing by the same rules. Because of this, the ability to attack the system will be minimized because competitors will not have the means to attack the system, similar to how the team will not have the means to assist the system. These design choices and stipulations lead the team to conclude that the attack surface of the design is effectively zero, and that only environmental effects on the sensors could jeopardize the design. These will be mitigated via extensive testing beforehand.

XI. GANTT CHART

The Gantt chart was laid out in a way to ensure that each team member would not be overloaded with multiple tasks within the same week. In saying this, each member has been distributed evenly so that every task is completed by the deadline. The tasks are also laid out in such a way that the basic task would get completed and then built on with more advanced tasks. For example, the shooting mechanism bead trajectory calculations are shown to be completed before the preliminary testing or model are completed. In this instance, the team needs to know the desired speed and distance the bead needs before knowing if the launching mechanism can achieve the distance. Similarly, the microcontroller preliminary testing needs to be completed before the team can model the system. Outlining the tasks in this way will help ensure the team is able to complete all tasks before the required deadline. The chart is attached in Figure 15.

XII. REFERENCES
[1] “Arduino Mega 2560 Rev 3,” arduino.cc, [Online]. Available: https://store.arduino.cc/products/arduino-mega-2560-rev3. [Accessed: Oct. 17, 2021].
[2] IEEE SoutheastCon, “2022 SoutheastCon Hardware Competition Rules,” ieeesoutheastcon.org, Sep. 3, 2021.
[Online]. | Available: | https://ieeesoutheastcon.org/wp-
content/uploads/sites/309/2022 SoutheastCon HardwareRules-Final.pdf [Accessed: Oct. 17, 2021].
[3]J. Gallant, “How to read DC motor & gear motor performance curves,” ISL Products International. [Online]. Available: https://islproducts.com/design-note/how-to-read-dcmotor-gear-motor-performance-curves/. [Accessed: Oct. 31, 2021].

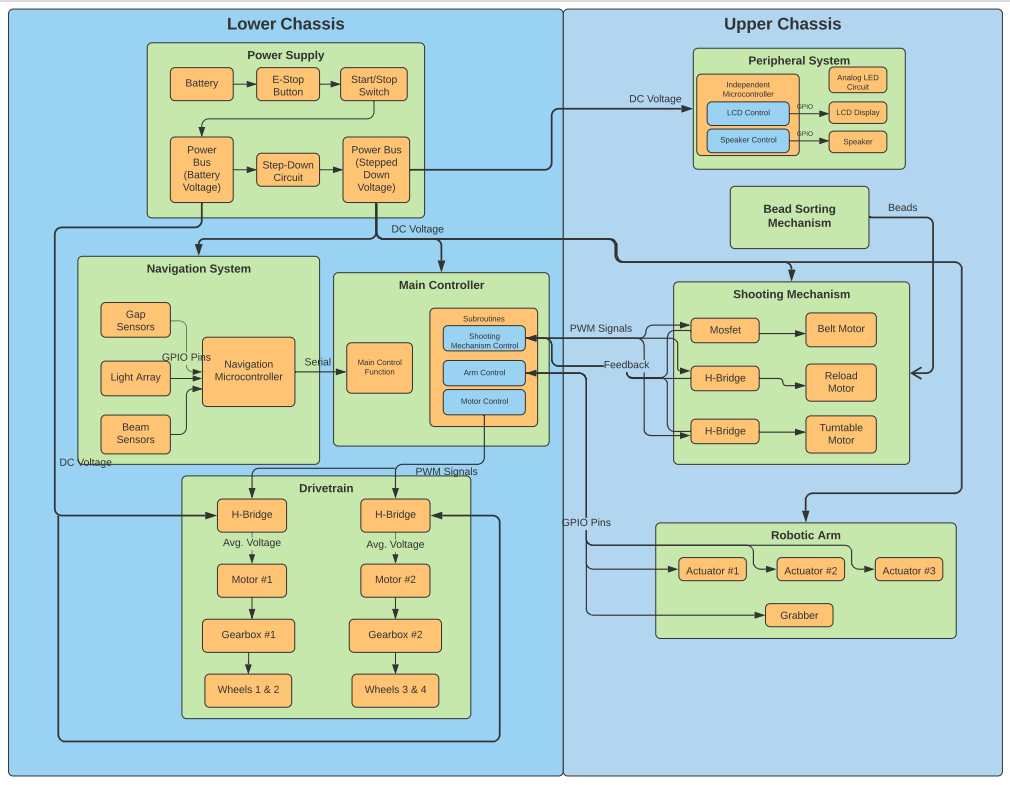
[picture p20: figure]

Fig. 14. Fulll block diagram

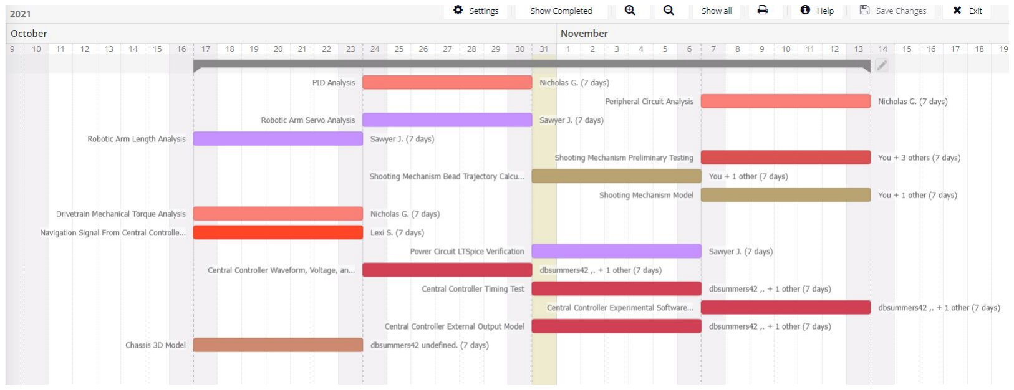
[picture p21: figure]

Fig. 15. Gantt chart

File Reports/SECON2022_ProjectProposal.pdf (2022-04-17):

# SouthEast Conference Robot Project Proposal

Chase Garner, Sawyer Hall, Lexi Sheeler, Daniel Summers
Electrical and Computer Engineering Department Tennessee Technological University Cookeville, TN
ncgarner42@tntech.edu, sjhall43@tntech.edu, aasheeler42@tntech.edu, dbsummers42@tntech.edu
I. INTRODUCTION
The goal of this project is to build an autonomous robot that
can | navigate | | an | L-shaped | | track | designed | | after | | a Mardi-Gras
decorated | | | street | within | a three-minute | | time | limit. | The | course
will | have | additional | | | challenges | | that | the | robot | can | complete | | for
extra | | points. | Initially, | | the | plan | is | to | build | the | robot | to | respond
to | manual | | commands | | to | assist | | with | | mechanical | | | errors, | and
then | move | on | to | complete | | autonomy. | | | The | team | consists | | of
two | computer | | engineers, | | | who | will | handle | | software | | and | mi-
cro-controllers, | and | two | electrical | engineers, | who | will | handle
power | and | controls. | | This | implementation | | | | | will | be | completed
no | later | than | March | 25, | 2022, | at | which | point | the | design | | will
be | finalized. | | | This | leaves | a week | for | final | | testing | | before | | the
competition | | | | begins | | on | March | 31, | 2022. | The | proposed | | budget
is | $2000, | but | this | number | | is | subject | | to | change | as | the | team
fulfills | | the | final | | design | | of the | | robot. | The | team | aspires | | to | revive
the | Tennessee | | Tech | IEEE | chapter | | and | inspire | | more | students
to | join | and | compete | | in | the | future.

II. BACKGROUND
The | competition | rules | referenced | herein | are | specified | by
the | IEEE | SECon | Hardware | Competition | guidelines | [1]. | The
competition | will | take | place | on | a | gameboard | constructed | from
a | single | piece | of 4’ | x | 8’ | plywood | decorated | like | a | Mardi-Gras
Street. | The | street | itself | will | be | a | painted | black | roadway | with
white | painted | center | lines. | The | black | street | will | measure | 16”
wide, | while | the | centerline | will | measure | approximately | 1”. | The
street | will | also | be | lined | with | obstacles | that | the | robot | must
avoid | while | navigating. | One | such | obstacle | will | be | a | single
powerline with two power line poles. The poles will be wooden
dowels | | that | measure | | 1.25” | | in | diameter. | | | | The | powerline | | | will | • • • • | Damage | | to | the | gameboard
connect | | the | two | dowels | | on | either | | side | of | the | street. | A | rope | | Venturing | | | or | falling | off | the | gameboard
will | be | used | | as | the | power | line | and | will | have | at | most | a 3” | | Touching | | the | robot | after | | hands | off
sag | that | the | robot | will | have | to | fit | under. | | The | street | will | also | | Remotely | | operating | | | | the | robot | after | hands | off
be | lined | with | 2” | barricades. | There | will | be | four | 2” | gaps | in | the
barricades that a randomly placed marshmallow will be pushed
through. Out of the four gaps, two of the gaps will be randomly
closed | off at | the | start | of the | round. | The | competition | organizers
have | specified | that | none | of the | gaps | will | be | within | four | inches
of | the | powerline | poles. | The | robot | must | stay | on | the | street;
however, | the | appendages | of | the | robot | are | allowed | to | extend
past | the | barricade. | Beyond | the | barricades | will | be | a | sidewalk
on | either | side. | The | sidewalk | will | contain | opportunities | to | earn
points. | One | opportunity | will | be | four | red | 16-ounce | solo | cups
placed | randomly | along | the | track. | The | red | cups | will | represent
trash | bins | along | the | sidewalk. | | Another | | game | mechanic | | will
be | three | randomly | | placed | and | vertical | | | fishing | | nets | measuring
8” | in | diameter. | | | The | last | component | | | of | the | sidewalk | | will | be
two | wooden | dowel | trees | measuring | | | in | 0.875” | diameter | | | and
2’ | in | height. | The | trees | will | have | a | limb | 21” | above | the | base
that | extend | | 6” | outward. | | Circular | | | bead | necklaces | | measuring | | | in
2.5”-3” | | diameter | | | will | be | placed | on | the | limbs. | The | gameboard
can | be | seen | in | Figure | | 1.
The | robot | itself will | | | be | constrained | | to | one | cubic | | foot | at | the
beginning | | | of | each | round; | however, | | it | may | extend | | beyond | | the
initial size constraint as long as obstacles are still avoided. The
robot | will | need | to | have | a | clear | start/stop | switch | for | operation
and | an | emergency | | stop | | switch. | The | robot | will | not | be | able
to | break | apart | or | have | any | aerial | or | flying | | components. | | | The
competition | | | | also | excludes | | any | use | of explosives, | | | | pyrotechnics,
or | toxic/corrosive | | | | | materials. | | | | The | team | is | responsible | | | for | pro-
tecting | | any | sensors | | from | potential | | | outside | | interference. | | | | The
gameboard | | will | be | elevated, | | so | precautions | | | must | be | taken | to
prevent | | the | robot | | falling. | | All | in | | all, | | the | | robot | will | need | to
present | no | harm | to | the | judges | or | any | spectators.
The | robot | will | also | have | tasks | to | complete | for | points | along
with | traversing | the | track. | The | point | system | can | be | seen | in
Figure | 2. | The | design | of | the | robot | should | maximize | the | pos-
sible | points | earned. | Overall, | the | team | will | need | to | efficiently
complete as many tasks as possible. The team will be penalized
1 | point | for | any | task | that | is | attempted | but | not | completed. | The
team | can | also | be | penalized | 5 | points | for | hitting | an | obstacle | and
10 | points | for | knocking | over | any | obstacle. | The | team | can | also
be | disqualified. | The | main | four | actions | that | will | disqualify | the
team | include:
The | team | can | utilize | the | point | system | in | Figure | 2 | to | earn
the | maximum | number | of points. | The | team | will | be | able | to | earn
1 | put | for | pushing | the | marshmallow | off the | roadway; | however,
the | marshmallow | must | not | leave | the | ground | while | being | re-
moved | from | the | track. | The | robot | can | earn | 1 | point | for | placing
the | beads | into | a | trash | bin | or | 2 | points | for | shooting | the | bead
into | a | fish | net. | The | team | will | also | obtain | 1 | point | for | each | trash
bin | or | fish | net | that | has | a | bead | in | it. | Beads | must | travel | an | aerial
distance | of | 4” | for | the | shot | to | count.
Aside | from | obstacles | within | the | course, | the | team | can | earn
points | by | adding | decorations | to | the | robot. | For | one, | the | team

will | need | to | decorate | | | the | robot | to | resemble | | | a | Mardi-Gras | | float.
The | team | can | earn | 2 | points | for | having | | a | display | | that | moves
mechanically | | | at | least | 4”. | The | team | will | earn | an | additional | | | 2
points | for | a light | up | display. | | The | team | can | also | earn | 2 | points
for | having | | a | speaker | on | the | robot | that | plays | a song.
Along | with | robot | and | gameboard | | specifications, | | | | the | compe-
tition outlines rules for the game. The team will have to follow
the | rules | to | ensure | | that | the | robot | is | not | disqualified. | | | The | com-
petition | | | will | have | three | rounds: | qualifying, | | | semi-finals, | | | and
finals. | | All | teams | will | compete | | in | the | qualifying | | | round. | The
top | twenty | teams | will | compete | | in | the | semi-finals | | | and | then | the
best four teams will compete in the final round. The qualifying
and | the | semi-finals | | | will | have | two | rounds. | The | best | score | out
of | the | two | | rounds | will | | be | used | for | | the | | overall | | | round. | The
team’s | round | time | will | be | used | if | the | robot | scores | the | max-
imum | number | | of | points. | Each | team | will | be | assigned | | a | play
order | | in | which | the | team’s | robot | will | compete. | | The | team | must
qualify 30 minutes prior to their scheduled play slot. From this
time, | the | team | will | not | be | able | to | make | any | adjustments | | | to
the | robot. | The | team | will | then | be | called | two | minutes | | prior | and
must | arrive | | within | the | two | minutes. | | Each | team | must | designate
a robot | handler. | | The | robot | handler | | is | the | only | person | | allowed
within | two | feet | of | the | gameboard. | | After | | arrival, | | the | team | will
have | one | minute | setup | | period | | before | | | the | | round | | starts. | The
judges | will | then | announce | | the | start | of the | | round. | At | this | point,
the | robot | handler | | will | push | the | start | button | | on | the | robot. | The
judges | will | signify | | the | end | of the | | round; | however, | | a judge | can
call | the | round | off | early | if | a team | member | | touches | the | robot.
The team is also allowed to call the end of the round in case of
an | emergency. | | The | team | is | also | required | | to | address | | the judges
following | | | the | IEEE | code | of conduct. | | | The | only | person | | that | can
address | | the | judges | is | the | team | captain | | for | written | | or | verbal
decision | | | | appeals. | | | The | appeals | | will | only | be | accepted | | within
five | minutes | | after | | the | team’s | score | is | displayed. | | If | the | appeal
is | declined | | the | team | will | be | deducted | | 50 | points. | Above | all,
the | team | is | expected | | to | act | in | a | calm, | polite, | | and | professional
demeanor.
Specific | | techniques | | must | be | utilized | | in | order | | to | successfully
implement | | | a design | | that | meets | the | functional | | requirements | | | of
the | competition. | | | | For | example, | | | specific | | protocols | | | must | be | fol-
lowed | to | interface | | | with | and | control | | DC | motors, | | such | as | pulse
width | modulation | | | | (PWM) | and | inverse | | kinematics. | | | Pulse | width
modulation is used in motor control ”by driving the motor with
a series | | of | ”ON-OFF” | | pulses | and | varying | | the | duty | cycle, | | the
fraction | | of | time | that | the | output | | voltage | | is | ”ON” | compared | | to
when | it | is | ”OFF”, | of | the | pulses | while | keeping | | the | frequency
constant” | | [2]. | This | ON-OFF | | ratio | | determines | | | the | power | sup-
plied to the motor, where a larger ratio of ON to OFF results in
greater | power | supply | | and | vice-versa. | | Inverse | | kinematics | | | refers
to | a mathematical | | | process | | used | to | calculate | | | the joint | | positions
needed | | to | produce | | a | specific | | endpoint | | position | | | [3]. | | Such | a
process | | may | be | used | in | the | design | | of | the | robot’s | arm | to | cal-
culate | | the | specific | | rotational | | | angles | | of connected | | | motor | | servos
by | simply | | providing | | | such | a | system | | with | a | desired | | endpoint
coordinate.
To | implement | the | autonomy | of | the | robot, | a | variety | of | sen-

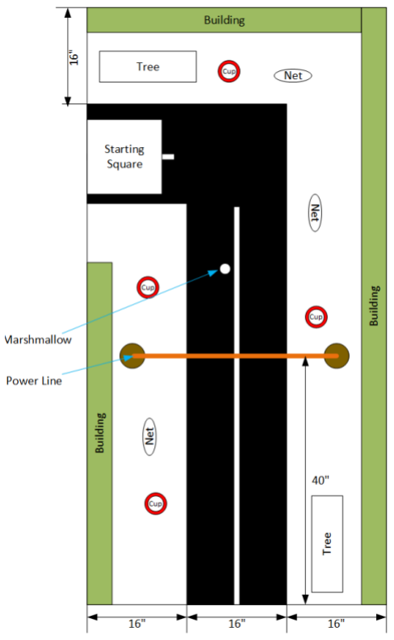
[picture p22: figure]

Fig. 1. Competition track layout.

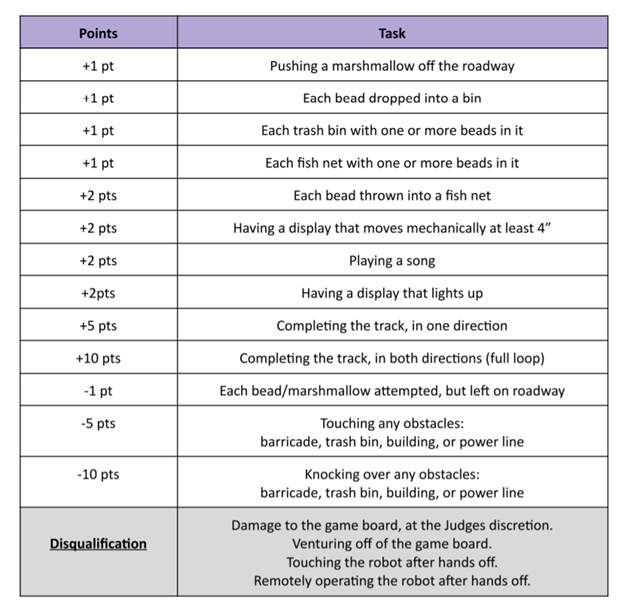
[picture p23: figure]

Fig. 2. Competition point breakdown.

sors | of | varying | | types, | such | as | radar, | lidar, | | infrared, | | and | laser,
may | be | utilized. | | Depending | | | on | the | type | of | sensor | | and | its | pur-
pose, | specific | | considerations | | | | must | be | taken | to | reduce | | interfer-
ence | and | poor | performance. | | | Such | complications | | | | may | include
lighting | | conditions, | | | erroneous | | | signals | | from | other | competitors
or | networking | | | equipment, | | and | flash | photography.

III. TECHNICAL OVERVIEW

This project will consist of a variety of sub-systems, with each system requiring its own specific hardware, software, testing/verification, and skills to be developed. Individual subsystems will then require interfacing to the central controller via standard protocols. These sub-systems must be outlined, designed, developed, and tested both independently and concurrently. By ensuring each sub-system complies to the standard interfacing protocols and meets the design requirements specified by the overarching system, each sub-system can be developed independently and then combined to complete the system. A high-level block diagram of the system is shown in
Appendix | A | below.
A. Central controller
In order to construct an autonomous robot, a central controller will be required to manage the underlying sub-systems and their function. This central controller is commonly attributed to possess the “intelligence” of a robot. This controller will be responsible for the decision making of the robot, as well as communicating the necessary actions and receiving input information from the various other systems. This unit will consist of either a microcontroller such as an Arduino or STM32 or a small “Card Computer” such as a Raspberry Pi. The skills required for the development of the central controller will be primarily software and programming based. A knowledge of microcontrollers, communication protocols, embedded systems, and operating systems will be vital for this component. Being the central system of the robot, the controller will have direct connections to each of the other subsystems. Each of these connections must be verified and confirmed to comply with the communication protocol used by the sub-system. Additionally, the decision-making process of the central controller must be validated using a testbench of input parameters.
B. Vision/Object Detection System
A vision or object detection system must be configured for the robot to autonomously navigate, identify objectives, and avoid obstacles. The two main components of this system will be the Sensor Hardware and the Detection Software. The complexity of this system will be dependent on the construction of these two components, and a variety of designs can be constructed using a varying level of both hardware and software complexity [4]. The vision system may be constructed using a small number of advanced hardware devices, which will then require more complex software to interpret and process the data. Inversely, a simpler software implementation may be designed that instead utilizes a large array of smaller, lower-function sensors. Once the specific design approach is determined, the necessary hardware and software requirements can be determined. Regardless of design, particular skills such as computer programming, hardware interfacing, and a knowledge of computer vision systems will be required. To test such a system, the interfacing between hardware elements must be verified. Also, the system must be tested in order to determine the accuracy of identifying different competition elements. Lastly, the information received by the Central Controller from the Detection Software must be compliant with the Central Controller’s decision-making process.
C. Motor Control System
While the Vision System and Central Controller will primarily be responsible for the decision making and autonomous function of the robot, separate hardware and software will be required to execute the functions of movement, object collection and distribution, etc. This hardware and software will constitute the Motor Control System, and it encompasses both the driving motors for moving the robot along the competition surface and the servo motors used by the robot to collect and place the game pieces in each objective. The Motor Hardware and Servos will be driven by Control Software. This software will receive the “decisions” made by the Central Controller and convert them into Pulse Width Modulation (PWM) signals to be sent to Motor Hardware [5]. The exact hardware requirements for this system will depend on the choice of drivetrain and the desired method of collecting and distributing the game pieces. Additionally, hardware such as gears, wheels, belts and various actuators may be required. Because of the nature of this system, knowledge of mechanical concepts will be required for the design of the motor hardware. Other skills such as specific knowledge of controller hardware, control systems, and the physical limitations of components will be necessary for the design of this system. Testing the system will consist of measuring the signals to be sent from the Control Software to the hardware to ensure they accurately match the desired PWM parameters. Additionally, the Motor Control System should be tested independently of the Central Controller and decision-making system via manual operation. By verifying the behavior of the Motor Control System using manual signals, similar behavior can be expected when the robot is configured to operate autonomously.
D. Power System
In order to power the various sub-systems on board the robot, a power system must be developed. This system will be responsible for supplying the correct DC Power directly to each sub-system. A battery will serve as the power supply, but the exact size and rating of the battery will be based on the specific power requirements of the other systems. Additionally, specific circuitry for charging the battery and regulating power output for certain applications will be required, and the proper safety measures (circuit breakers, emergency stop switches, and fuses) must be integrated into the power supply system. A knowledge of batteries, power needs, PCB design, and proper electrical safety measures will be needed to design this system. Safety measures will include proper grounding and insulation and over current protections [6]. The power output by the system will have to be tested and verified that it meets the power consumption needs of the device. Extraneous systems must also be tested to ensure their maximum power consumption and current draw do not exceed the safety limitations of the power system. Lastly, safety measures such as fuses and emergency stops should be tested to ensure the proper behavior is exhibited in the event of a catastrophic failure.
E. Peripheral System
While not necessary to the autonomous operation of the robot, the competition outlines additional consideration for designs that include a display, music, and decorations. The Peripheral System will be responsible for controlling these additional functions. In order to complete these competition requirements, an LCD Display, speaker for playing music, and LED lights will be required. Additionally, software must exist in the Central Controller that controls these peripherals. Knowledge of these devices, file storage for audio files, and artistic creativity will be needed for this system. Testing methods will consist of verifying the hardware and software comply with the competition regulations and ensuring the peripherals do not interfere with the primary function of the robot.
F. Chassis
The chassis will serve as the housing for the other various sub-systems of the robot. The chassis must allow for access to the various sub-systems’ ports and connections to allow for quick repair in the event of a minor failure. Additionally, the chassis must contain the start and emergency stop buttons, and they must be clearly marked. The chassis will also be responsible for housing the mechanism that will hold the game pieces once they have been collected. Knowledge of materials, 3D modelling software, and 3D printing will be required to design and build the chassis. The chassis must also be tested to ensure it is structurally sound enough to handle the forces of the Motor System, and it must be verified to fit within the size constraints as outlined by the competition.
G. Common Requirements
While some aspects of each sub-system’s design will be unique, many commonalities will exist between sub-systems as well. Beyond basic electrical components and a general understanding of Electrical and Computer Engineering concepts, specific hardware components, technical skills, and testing methods will be shared across many aspects of the project. Components used throughout the design but are not specific to a given subsystem include:
- Wiring
- Fastening hardware (screws, bolts, nuts, etc.)
- Electrical connectors
- An accurate model of the competition environment and all associated components

Skills needed across each subsystem include:
- Component selection and testing
- Simulation
- Programming experience (languages may include C, C++, Python, etc.)
- Electrical wiring and soldering
- Operation of lab equipment (digital multimeter, oscilliscope, function generator)
- Schematic capture
Testing Methods to be utilized across the project will include:
- Simulation and verification of measured values
- Input and output signal analysis using lab equipment as a stand in for other subsystems
- Software testbenches and code review
- Inter-system interface verification
Additionally, a final system checkout will be necessary to ensure the hardware has met the competition specifications and is functionally ready for the SoutheastCon Competition. In this final checkout, the entire system will be compared to the desired behavior and the competition specifications. The robot will also be required to conduct a “live” competition environment demo.

IV. OUTCOMES AND DELIVERABLES
Coming out of this project, members will have experience working on a real-world engineering project. This includes project management, working as a team, design process, and problem solving. Members will also broaden their knowledge of engineering topics related to their discipline. The team members will gain a vast knowledge of robotics, an area to which they have no knowledge.
The principal deliverable of this project will be a fully autonomous robot. Ideally, it will perform all tasks outlined in the project specifications and will adhere to competition rules outlined before. Of course, many small deliverables have been outlined by the team, which is integrated into the project timeline. Deliverables are as defined in by the measures of success.
V. OBSTACLES
The largest obstacle in this project is that members of the team have little to no experience building and programming a robot; however, members have vast knowledge of electrical and computer engineering topics that will provide a strong foundation for overcoming the task at hand. Members have experience with programming, power, controls, electrical components, isolated testing, microcontrollers, and computer aided design (CAD). While these areas will prove useful, there are still some skills, such as 3D printing, communication protocols, and autonomous/sensor programming, that the team is not experienced in. Overcoming this problem will require research in areas with no experience and continued learning in areas where members already have experience.
Due to the ongoing Covid-19 pandemic, there is a computer chip shortage [7]. This may lead to supply issues for necessary computing components. To resolve this, the team will complete design work as soon as possible to ensure early ordering of chips. One obstacle the team has already encountered is scheduling conflicts, and this is expected to continue as the project progresses. Another obstacle will be the possibility of purchasing components that do not perform their expected behavior. This is expected due to the lack of experience by the team, and it must be mitigated by thorough testing and allowing for enough time to select and order replacement components should the need arise.
Additional obstacles present themselves in the project speci-
fications. | The | arm | must | reach | the | branch | of the | trees, | a | height
of | 21”, | but | the | power | line | is | 2’ | tall | with | up | to | 3” | of | verti-
cal | slack. | This | means | the | arm | will | need | to | extend | to | retrieve
the | beads | from | the | tree, | and | then | retract | to | avoid | hitting | the
power | line. | The | robot | will | also | need | to | differentiate | between
the | nets | and | the | power | poles, | but | most | sensors | are | unable | to
detect | soft | materials, | so | the | team | will | need | to | come | up | with | a
different | method | of | detecting | where | to | shoot | the | beads. | This
presents | another | problem; | the | shooting | apparatus | will | need
to | have | enough | friction | to | launch | the | beads, | while | avoiding
objects | on | the | sidewalk. | Although | the | rules | specify | that | the
robot | must be | contained in | one | cubic | foot | at the | start, | doing | so
will not allow the robot to turn without touching the barricades
because | the | diagonal | dimension | is | slightly | larger | than | 16”.

VI. MEASURES OF SUCCESS

The team’s success will be divided into two parts: engineering success and competitive success. The engineering measures of success will be evaluated based on meeting the specifications and objectives of the competition while staying within the constraints set forth by the SECon organization. The team is expected to carry out many test-runs and evaluations throughout the process of building the robot, and many of these tests are expected to be reliant on trial and error. Whether or not these test-runs are deemed successful depends on if the robot is able to perform as expected given the objectives as well as the constraints.
One | of | the | most | crucial | specifications | to | which | the | robot
must | adhere | is | the | size | spec. | The | competition | rules | state | that
the | robot | must | be | contained | within | one | cubic | foot. | The | team
will | have | to | take | this | into | consideration | throughout | the | entire
design | process. | Abiding | to | this | spec | is | crucial | to | the | team’s
competitive | success | as | not | doing | so | will | result | in | instant | dis-
qualification.
The building process of the robot is expected to consist of many stages. For example, the team believes that the first objective is to build a robot that can move manually. The manual motion of the robot will need to be thoroughly tested.
To | carry | out | testing | of | the | robot’s | mobility, | a | replica | of | the
competition | track | will | be | necessary. | Once | the | drivetrain | is | de-
signed | and | assembled, | the | team | will | carry | out | tests | using | the
track. | The | first | tests | that | the | team | conducts | will | be | manually
moving | the | base | of | the | robot, | as | well | as | testing | its | maneu-
verability. | Manual | testing | of the | drivetrain | will | consist | of giv-
ing | the | main | microcontroller | velocity | and | direction | commands
that | will | be | translated | | to | the | motor | | via | an | intermediary | | motor
driver. | The | main | goal | of these | | tests | is | to | prove | that | the | method
of motor control is feasible and the robot is in fact able to fully
navigate | the | track.
Line | detection | | | will | be | another | | important | | | aspect | | of | the | en-
gineering | | | success | | of | this | project. | The | robot | will | need | to | be
able | to | follow | | a | white | line | on | the | track | at | a reasonable | | | speed
without | | deviating | | | | too | much | from | the | center. | | To | accomplish
this, | the | robot | will | have | to | be | self-correcting. | | | | The | team | will
once again use the replica of the competition board to fine tune
the | navigation | aspect | of | the | robot. | The | team’s | goal | is | for | the
robot | to | complete | the | entire | track | and | all | tasks | without | losing
its | position | on | the | line. | It | is | desired | that | the | robot | will | be | able
to | move | at | a | velocity | of | up | to | 2ft/s | without | deviating | from
the | line. | This | will | require | the | team | to | conduct | many | trials | to
tune | the | self-correcting | aspect | of | the | robot | that | will | focus | on
finding | the | correct | PID | coefficients | to | program | into | the | motor
interface.
One | aspect | of | the | competition | is | to | identify | and | safely | re-
move | a | marshmallow | from | the | road. | In | order | to | do | this, | the
robot | must | identify | the | marshmallow | and | the | appropriate | gaps
in | the | barricades. | During | trial | runs, | the | robot | should | correctly
identify | these | components | of the | gameboard | and | complete | the
task | on | at | least | 85% | of | attempts.
Bead | obtainment | and | placement | are | the | main | tasks | that | the
robot | will | need | to | excel | | at, | and | as | such | the | team | will | need
to | ensure | | that | the | robot | collects | | as | many | beads | as | possible.
Collecting | | | beads | will | require | | some | sort | of | armature, | | | and | the
team | will | need | to | develop | | a finely | tuned | system | | to | carry | out
this | task. | The | team | would | like | to | be | able | to | collect | | 90% | of
the | available | | beads | and accurately | | | | launch 95% | | of the | | collected
beads | into | the | nets. | Testing | | this | system | | will | require | | that | the
team | hang | beads | in | the | same | manner | | that | they | will | be | hung
during | | the | competition. | | | | After | | this, | the | team | will | focus | | on | cre-
ating | | the | most | efficient | | | system | | possible | | | to | obtain | | the | beads
using | | the | designed | | armature. | | | In | addition, | | | sorting | | the | beads | is
also | a | point | of | interest | | | for | the | team’s | success. | | It | is | desired
that | the | obtained | | beads | be | separated | | into | three | containers, | | | i.e.,
equal | to | the | number | of nets | along | the | track. | Because | there | are
no | additional points | available | for the | number of beads | that | end
up | in | nets, | the | team’s | goal | is | that | each | container | contains | at
least | one | band | of beads. | Finally, | the | time | it | takes | to | obtain | all
of | the | beads | will | also | need | to | be | minimized. | The | time | goal
for | obtaining | beads | at | both | ends | of the | track | is | 20 | seconds | for
each tree. In the case of firing the beads into nets, the team has
set | a | time | goal | of 20 | | seconds. | | This | time | includes | | the | moment
a net | is | detected | | to | the | moment | | that | the | robot | is | driving | | again.
With | the | target | | of | shooting | | beads | into | all | 3 | nets, | this | gives
the | robot | a | cumulative | | | | time | of 1 | | minute | to | complete | | this | task.
When | adding | together | the | times | for | obtaining | beads | as | well
as | launching | them, | the | robot | has | 1 | minute | and | 40 | seconds | in
total, | giving | the | robot | an | additional | 1 | minute | and | 20 | seconds
to | traverse | the | track | and | attempt | to | move | the | marshmallow.
Target | detection, | i.e., | knowing | when | to | shoot | the | beads, | is
crucial | for | the | success | of | this | project. | It | is | highly | undesirable
for | the | robot | to | launch | the | beads | at | the | wrong | time/target. | As

such, | the | targeting | | system | | and | launching | | mechanism | | will | need
to | be | heavily | tested. | Once | the | motor | | control | | has | been | tested
and | tuned | manually, | the | robot | must | use | sensors | | in | order | | to
navigate | and | control | the | motors | itself. | The | goal | is | that | when | a
net | is | detected, | | the | robot | will | line | itself up | | | with | the | target | | and
fire | the | beads | as | closely | to | the | center | | of | the | net | as | possible.
This | will | require | | that | the | team | sets | up | nets | along | the | replica
track | and | allows | | the | robot | to | attempt | | to | detect | | them. | Routines
will | be | written | | within | | the | | main | processor | | | that | will | | control
the | recognition | | | of | the | nets | and | the | aiming | | of | the | launching
mechanism. | | The | detection | | | rate | of | nets | is | desired | | at | 100%, | as
it | is | more | advantageous | | | | to | launch | beads | into | all | of | the | nets.
This | will | require | | precise | | mounting | | of | the | sensors | | to | the | robot
chassis and documenting detection rates in order to get as close
to | this | goal | as | possible.
If the team is able to build a robot that incorporates all of the objectives set forth by the competition, and these functionalities are verified and determined to be fulfill the constraints, the overall effort of the team, as well as the final product, will be deemed a success.
The team’s success will be further evaluated on its ability
to produce a product that performs well in competition. | The
target | | of | the | team | is | to | accumulate | | | | the | maximum | | available
points | for | traversing | | the | track | in | both | directions, | | | launching
beads | into | all | of | the | available | | nets, | including | | | all | of | the | pe-
ripheral/aesthetic | | | | tasks, | and | avoiding | | touching | | any | obstacles
or | damaging | | | the | track. | Adding | the | available | | points | for | these
tasks | | give | the | team | | a target | | | of | | obtaining | | | 40 | points. | If | the
final | | product | | | meets | | the | | measures | | | of | success | | | highlighted | in
the | previous | | | sections, | | the | overall | | effort | | of | the | project | will | be
considered | | | a success.

VII. BUDGET

This budget will serve as a preliminary estimate of the cost of the project and a metric to determine the project’s financial feasibility. Exact component costs will become finalized in the later design phases as more specific details are known. The budget is broken down on a sub-system by sub-system basis. Each component price is listed as a range of the unit price. The total component cost range is then calculated by multiplying the lowest quantity by the lower bound of the range and the largest quantity by the upper bound. Total ranges for each subsystem, and the system total are then calculated by summing the lower and upper bounds of each component, respectively.
A | 50 | percent margin of error is then added to the total to
account for additional components and price changes/shipping costs. The final grand total is then listed at the bottom of the table.
| | VIII. PROJECT SCHEDULE

The project timeline is based on the outline provided in the course syllabus. It is comprised of three overarching sections: Design Phase One, Design Phase Two, and Development/Testing. Each of the three main sections have various tasks and deadlines within them.

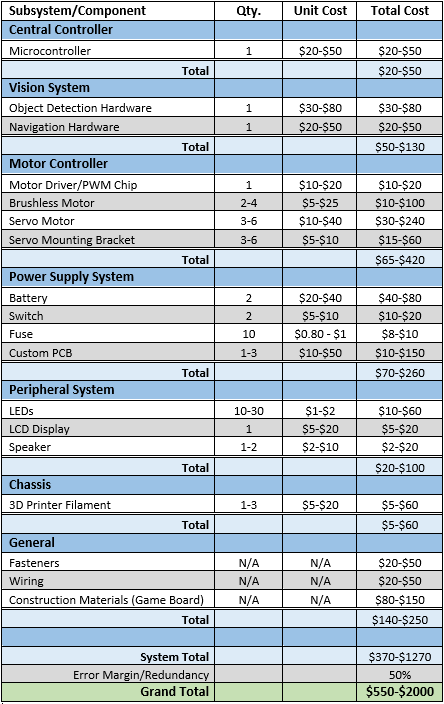
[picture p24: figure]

Fig. 3. Itemized cost breakdown.

During Design Phase I, the team will independently research the various subsystems outlined in the proposal and try to come up with the most viable, cost-effective solution. Although research will be conducted independently, it is important that the team members discuss what they find during team meetings in order to address issues of compatibility, cost, etc. Team assignments for the preliminary research phase are as follows: Daniel (Microcontrollers), Lexi (Vision System and Peripheral Systems), Sawyer (Power Distribution), and Chase (Motor Control/Drivetrain). Preliminary research should be completed along with a draft for Design Phase I by October 4th.
After the preliminary research and draft have been completed, the team will begin work on finalizing the first design for Design Phase I. This phase will be where the team discusses the viability and compatibility of each of the members’

findings in the previous phase. Design Phase I will see the team have a general idea for a solution as well as having selected the parts that will comprise the main subsystems. Design Phase I should be completed and finalized by October 18th.
Design Phase II is where the team will begin the detailed design and analysis of their proposed solution from Design Phase I. During this phase, the team will have already finalized all of the various parts that will be used in the design and will be working on the interfacing of the subsystems. This phase will see the team design the chassis and wheelbase, as well as complete the wire layout. The team should have a draft by November 24th. Following the draft of Design Phase II, the team will need to begin ordering parts. As of the creation of this proposal, the team’s designated parts acquirer will be Sawyer. The team will need to have their final design verified before moving on to the final phase. The final draft of Design Phase II will be completed by December 6th.
Due to Christmas break, Development and Testing will begin on January 10th, 2022. It is expected that all parts will have been ordered prior to this stage. This phase will see the team actualize its design. During this phase, the team will get the various subsystems of the design to at first work independently, and then as a unit. Although it is expected that each team member will play a role in all aspects of development, they will also have aspects of the product that they are considered responsible for. Daniel will oversee interfacing all subsystems with the central controller. Lexi will be responsible for programming the vision system and peripherals. Sawyer will oversee power distribution and wiring. Finally, Chase will be responsible for programming the motor controllers and building the drivetrain system/chassis. The hard deadline and competition date of this project is March 31st, 2022; however, the team should have a functioning product that meets competition specifications by March 25th.

IX. BROADER IMPACTS

It is possible that this project will have some effects on the school, including its perception throughout the region. Throughout the design and building process, it is expected that the team will take on some members from the IEEE chapter in small capacities. A project such as this has the potential to attract current members as well as new members to the chapter. In addition, the team performing well in competition will reflect well on the school, specifically Tennessee Tech’s Electrical and Computer Engineering program. Performing well in competition may catch the attention of prospective students who are interested in engineering and will make a case for what Tech’s engineering program has to offer compared to many other programs in the region. In addition, it may open other opportunities for future capstone groups to participate and compete in similar competitions. Furthermore, this project may open a door to integrating automated vehicles on Tennessee Tech’s campus. Automated vehicles are already being used on some campuses in the United States. For example, the food delivery company Grub-Hub has partnered with 250+ college campuses to implement

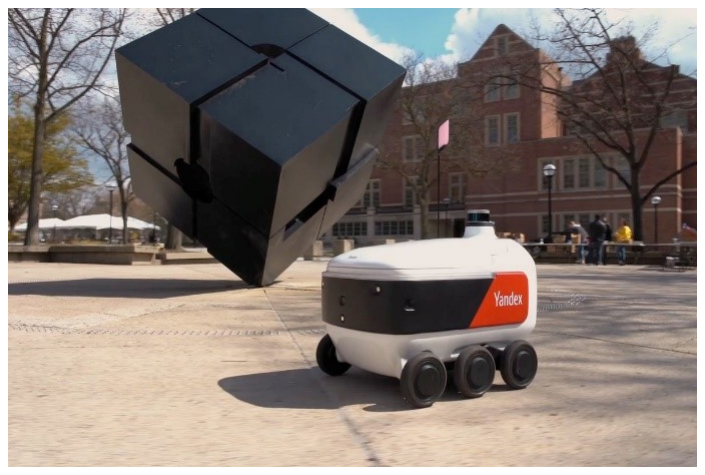
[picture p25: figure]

Fig. 4. GrubHub automated food delivery vehicle.

small, automated food delivery vehicles. Food delivery is just one of many opportunities to integrate these vehicles. Autonomous vehicles may also be used in sanitation, tours, crime prevention, etc. Of course, with increasing automation, there is the potential to eliminate some jobs. As in the GrubHub example, there are inevitably some food delivery drivers that are going to be displaced by this new technology. In the example of sanitation and tours, there are currently full time as well as student workers who handle these jobs. The ethical questions of this technology will need to be answered as it becomes a more viable solution for colleges across the country. There is also the question of safety in implementing these vehicles on campuses. Currently, Tech’s campus sees considerable car traffic. Autonomous vehicles have the potential to pose a hazard to divers on campus. As Tech becomes a more foot-oriented campus, as is outlined in the “Master Plan,” these risks will be reduced considerably.

X. REFERENCES
[1] IEEE SoutheastCon, “2022 SoutheastCon Hardware Competition Rules,” ieeesoutheastcon.org, Sep. 3, 2021.
[Online]. | Available: | https://ieeesoutheastcon.org/wp-
content/uploads/sites/309/2022 SoutheastCon HardwareRules-Final.pdf [Accessed: Sept. 19, 2021].
[2] | Electronics | Tutorials, | “Pulse | Width | Modula-
tion,” | electronics-tutorials.ws. | [Online]. | Available:
https://www.electronics-tutorials.ws/blog/pulse-widthmodulation.html [Accessed: 10/7/2021].
[3] A. Owen-Hill, “Inverse Kinematics in Robotics: What You Need to Know,” robodk.com, Jun. 4, 2021 [Online]. Available: https://robodk.com/blog/inverse-kinematicsin-robotics-what-you-need-to-know/ [Accessed: Oct. 7, 2021].
[4] “20 + Raspberry Pi Tutorials in Computer Vision,” intorobotics.com, August 3, 2015. [Online]. Available: https://www.intorobotics.com/20-hand-picked-raspberrypi-tutorials-in-computer-vision/[Accessed: Sept. 19, 2021].
[5] FIRST Robotics, “Using Motor Controllers in
Code,” | docs.wpilib.org, | 2021. | [Online]. | Available:
https://docs.wpilib.org/en/stable/docs/software/actuators/usingmotor-controllers.html [Accessed: Sept. 19, 2021].

[6] | L. | Benson | and | K. | Reczek, | “A | Guide | to
United | States | Electrical | and | Electronic | Equipment
Compliance | Requirements,” | National | Institute | of
Standards | and | Technology, | 2020.[Online]. | Available:
https://doi.org/10.6028/NIST.IR.8118r2 [Accessed: Sept. 19, 2021].
[7] | C. | Baraniuk, | “Why | is | there | a | chip | short-
age?,” | BBC | News, | 2021. | [Online]. | Available | at:
https://www.bbc.com/news/business-58230388[Accessed: September 15, 2021].

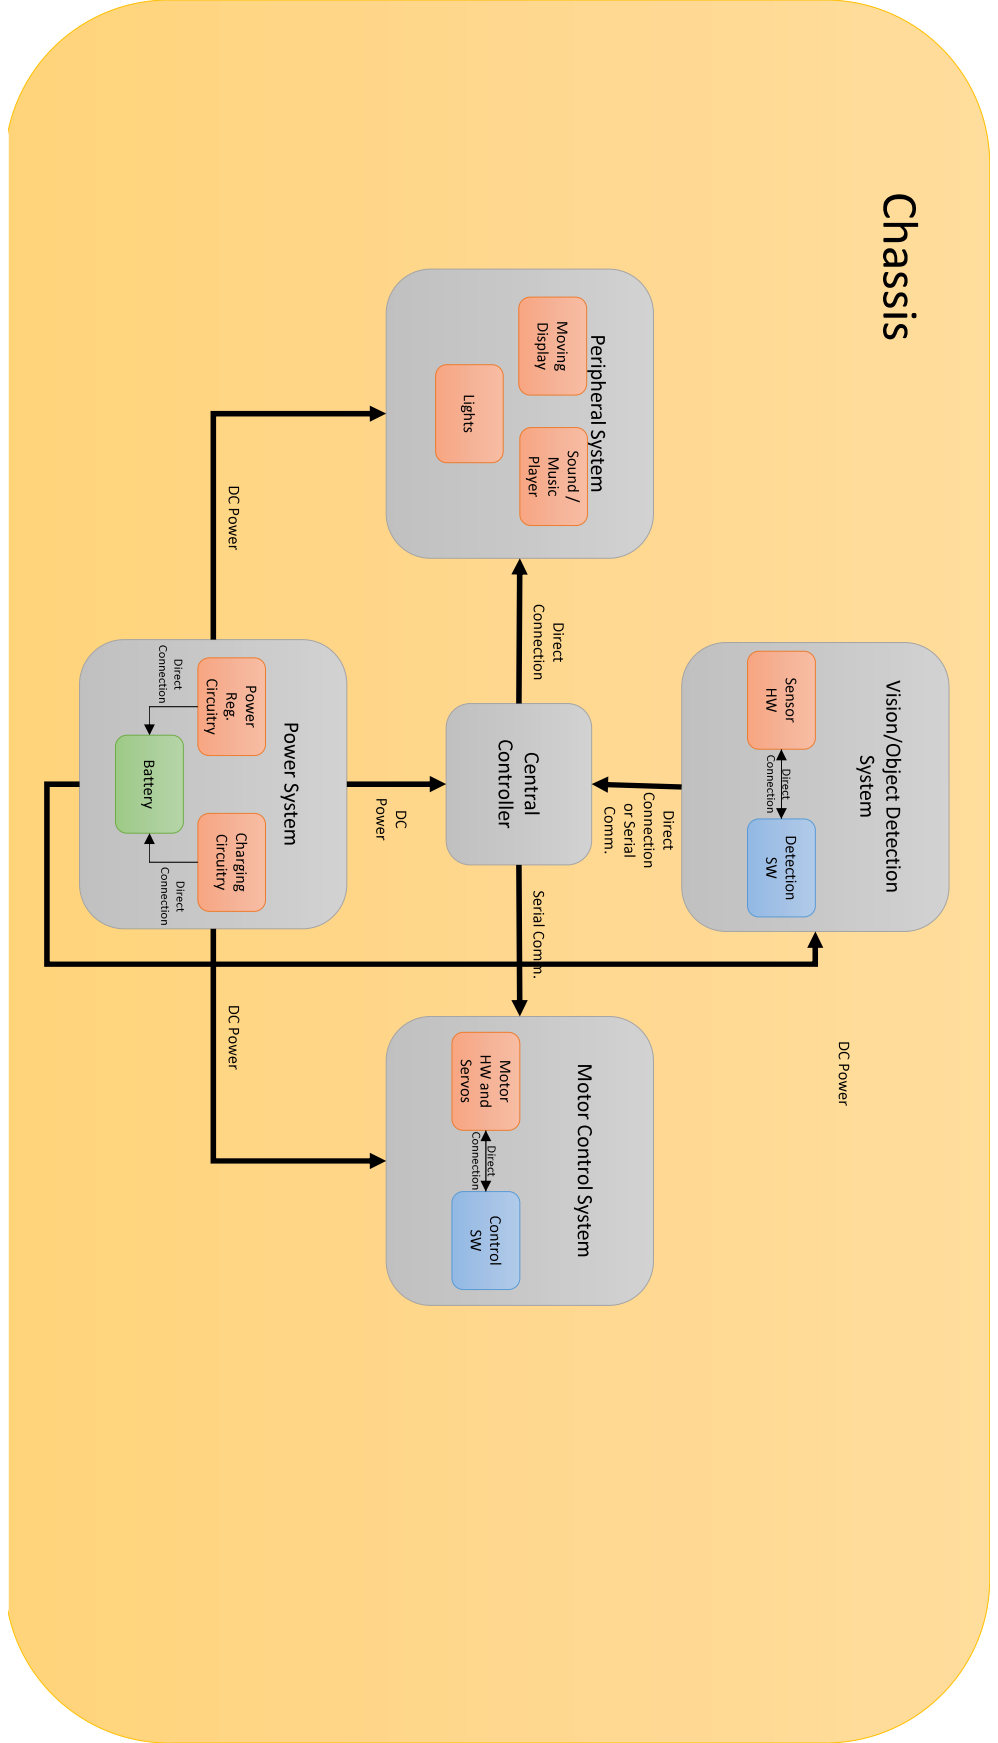
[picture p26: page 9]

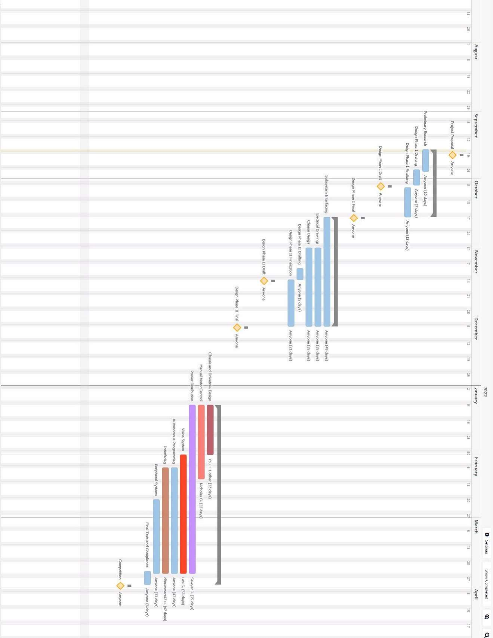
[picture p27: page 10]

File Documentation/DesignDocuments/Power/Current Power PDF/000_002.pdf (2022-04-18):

000-002

# | Product Name | Quantity | # | Product Name | Quantity

1 | LiFePO4 Battery 12 V 6.6Ah | 1
2 | Power Bus | 3
3 | Buck Convertor | 3
4 | Raspberry Pi 4B | 1
5 | USB-C cord to Raspberry Pi | 1
6 | Adafruit 16-Channel 12-bit PWM/Servo Shield | 1
7 | H-Bridge L298N Motor Drive Controller Board | 3
8 | Arduino Mega 2560 | 2
9 | Arduino Mega 2560 Power Cord | 2
10 | Boost Converter | 1
11 | Decoupling Capacitance | 3
12 | Switch | 2
13 | 2-Channel Emergency Stop | 1
14 | Line Following Array | 3

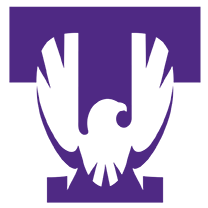
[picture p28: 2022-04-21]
Software/Raspberry Pi/tech.bmp

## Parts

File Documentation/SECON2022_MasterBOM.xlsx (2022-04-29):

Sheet: Master BOM
Product Name | Description | Part Number | Manufacturer | Unit Price | Quantity | Total Price
Arduino Mega 2560 Rev 3 | Main Microcontroller | A000067 | Ardunio | 34.25 | 1 | $34.25
Raspberry Pi 4 8GB | Navigation Computer | B08956GVXN | Raspberry Pi | 149.99 | 1 | $149.99
Clear Scratch- and UV-Resistant Cast Acrylic Sheet 12" x 24" x 1/4", Fluorescent Green | Chassis Acrylic ((Bottom and Turn Table) | 85635K531 | McMaster-Carr | 22.18 | 2 | $44.36
Clear Scratch- and UV-Resistant Cast Acrylic Sheet 12" x 24" x 1/8", Fluorescent Green | Chassis Acrylic (Vertical Faces) | 85635K451 | McMaster-Carr | 16.46 | 2 | $32.92
Pack of 100 Black-Oxide Alloy Steel Socket Head Screw 2-56 Thread Size, 1/4" Long | Chassis Fasteners | 91251A077 | McMaster-Carr | 8.32 | 1 | $8.32
Pack of 50 Brass Screw-to-Expand Inserts for Plastic, 2-56 Thread Size, 0.156" Installed Length | Mounting Inserts for Chassis | 92395A111 | McMaster-Carr | 12.06 | 1 | $12.06
USB Camera V2 module for Raspberry Pi | Navigation Cameras | IMX219 mini | Arducam | 29.99 | 2 | $59.98
HCSR04 Ultrasonic Distance Sensor | Navigation Ultrasonic Sensors | HC-SR04 | Elegoo | $4.99 | 2 | $9.98
IR infrared Distance Sensor | Navigation Infared Sensors | GP2Y0A21YK0F | Sharp/Socle | 8.99 | 4 | $35.96
Bead Necklaces | Game Board Material | WM320382 | Walmart | 8.12 | 1 | $8.12
Black Gloss Paint | Game Board Material | 1974502 | Home Depot | 11.98 | 2 | $23.96
White Gloss Paint | Game Board Material | 1993502 | Home Depot | 11.98 | 2 | $23.96
Solo plastic cup | Game Board Material | SCCP16R | Office Supply | 9.87 | 1 | $9.87
Frabill Fishing nets | Game Board Material | 16494432 | Walmart | 4.96 | 3 | $14.88
Wooden Dowel (1.25x1.25x48) | Game Board Material | 10001811 | Home Depot | 6.98 | 1 | $6.98
String | Game Board Material | PA-7211 | Home Depot | 3.98 | 1 | $3.98
Wooden Dowel (0.875x0.875x48) | Game Board Material | 10001807 | Home Depot | 5.1 | 1 | $5.10
Straight Peg Hook 0.25" Peg | Game Board Material | 18035 | Home Depot | 0.98 | 2 | $1.96
Marshmallows | Game Board Material | 51923014 | Walmart | 2.62 | 1 | $2.62
Lynxmotion AL5D PLTW Robotic Arm - Assembled | Robotic Arm Assembly | RB-Lyn-958 | Lynxmotion | 399 | 1 | $399.00
Adafruit 16-Channel 12-bit PWM/Servo Shield - 12C interface | Robotic Arm Servo Controller | 1411 | Adafruit | 17.5 | 1 | $17.50
LiFePO4 26650 Battery: 12.8V 6.6Ah | Robot Battery | CU-J961 | BatterySpace | 120 | 2 | $240.00
Smart Charger (3.0A) for 12.8V LiFePO4 Battery | Battery Charger | CH-LF1283 | BatterySpace | 35.95 | 1 | $35.95
Evemodel 2pcs 12 Position Power Distribution Board | Power Bus | B08Q34RGM8 | Evemodel | 9.49 | 3 | $28.47
DC to DC Converter and Switching Regulator Module | Buck-Boost Converter | UWE-12/10/Q12PB-C | Murata Power Solutions | 55.99 | 1 | $55.99
DC-DC Buck Converter | Buck Converter | LM2596S | Frienda | 15.99 | 1 | $15.99
AC DC Switching Power Supply Wall Adapter 12V 6A | Wall Wart for Testing | B08865VM9V | ZUEXT | 16.99 | 1 | $16.99
18 AWG DC Power Cable | Wire Adapters | B09H4B32CR | VWEICYY | 5.99 | 1 | $5.99
Solder-able Breadboard Gold Plated Finish Proto Board PCB | Filter Prototype Board | K12 | Gikfun Store | 10.28 | 1 | $10.28
Aluminum - Polymer Capacitor 33uF | Filter Component | 16SVPB33M | Digi-key | 1.79 | 6 | $10.74
Aluminum - Polymer Capacitor 220uF | Filter Component | PCV1C221MCL1GS | Digi-key | 3.29 | 6 | $19.74
Fixed Inductor 12uH | Filter Component | SRR1280-120M | Digi-key | 1.36 | 6 | $8.16
Schottky Diode | Power Switch Protection | SR806 A0G | Digi-key | 1.19 | 3 | $3.57
Ceramic Capacitor 6 pack 0.1uF | Filter Component | 2451 | Pololu | 0.99 | 3 | $2.97
1 Channel Switch | Start/Stop Switch | S6AW | Digi-key | 14.85 | 2 | $29.70
2 Channel Emergency Stop | Emergency Stop | B07NP44T74 | TWTADE | 12.99 | 1 | $12.99
Adafruit "Music Maker" MP3 Shielf for Arduino w/3W Stereo Amp -v1.0 | Peripheral Audio Shield | 1788 | Adafruit | 34.95 | 1 | $34.95
DiCUNO 200pcs 3mm LED Assorted Light Emitting Diodes Diffused 2pin Round UV White Red Yellow Green Blue Warm White Pink Orange Chartreuse Kit Box | Peripheral LEDs for Decoration | US 3MM-10T-200 | DiCUNO | 7.99 | 1 | $7.99
DSD Tech 1.8 inch TFT LCD Display Module with SPI Interface for Arduino and MCU | Peripheral Screen | B07WDJ3TV6 | DSD TECH Store | 9.99 | 1 | $9.99
Arduino Uno REV3 [A000066] | Peripheral System Microcontroller | A000066 | Arduino | 20.98 | 1 | $20.98
10:1 Metal Gearmotor 37Dx50L mm 12V (Helical Pinion) | Shooting Mechanism Driver Motor | 4748 | Pololu | $24.95 | 1 | $24.95
Machine Screw: M3, 8mm Length, Phillips (25-pack) | Motor Mounting Screws | 1076 | Pololu | $1.29 | 1 | $1.29
Light Duty Mounted Ball Bearings with Two-Bolt Flange | Shooting Mechanism Bearings | 4575N32 | McMaster-Carr | $9.56 | 3 | $28.68
3/16" Rotary Shaft | Shooting Mechanism Shaft | 1327K53 | McMaster-Carr | $8.02 | 1 | $8.02
8-32 Thread Insulating Rivet Nuts | Shooting Mechanism Adjustment Pieces | 93495A130 | McMaster-Carr | $7.88 | 1 | $7.88
18-8 Stainless Steel Pan Head Phillips Screw | Bearing Mounting Screws | 91772A194 | McMaster-Carr | $10.86 | 1 | $10.86
4mm to 5mm Set Screw Shaft Coupler | Shooting Mechanism Motor Coupling | RB-Sct-1368 | ServoCity | 4.99 | 1 | $4.99
Parallax (Futaba) Continuous Rotation Servo | Shooting Mechanism Reloading Motor | RB-Plx-180 | Parallax | 19.95 | 1 | $19.95
6 Inch Wide PVC 120 Cover One Side Black Conveyor Belt (5 Foot Length) | Shooting Mechanism Belt | ‎ B08GTV6DGD | Rubber and Accessories | 20.98 | 1 | $20.98
Hitec HS-645MG Servo Motor | Turntable Motor | RB-Hit-29 | Hitec | $34.99 | 1 | $34.99
Lynxmotion Base Rotate Kit (no servos) ***10 lbs | Turntable Mount | RB-Lyn-211 | Lynxmotion | $19.95 | 1 | $19.95
#4 x 3/8"Phillips Head Self-Tapping Screws | Turntable Mounting Screws | 311371959 | Prime-Line | $7.58 | 1 | $7.58
12 V DC Geared Motor | Drivetrain Motor | Pololu item #: 4743 | Polulu | $24.95 | 5 | $124.75
M3 Screw Set | Drivetrain Motor Mount Screws | Pololu item #: 1075 | Generic | $0.99 | 1 | $0.99
Mecanum Wheel 4 Pack | Drivetrain Wheels | FT-MECANUM-SET-V2 | Fingertech Robotics | $70.94 | 1 | $70.94
L298N H-Bridge Motor Driver (2 Pack) | Drivetrain H Bridges | B01M29YK5U | Qunqi | $8.99 | 2 | $17.98
Additional Hardware, Electronic Components, Items Purchased by Team Members |  |  |  | $141.52 | 1 | $141.52
 |  |  |  | Totals | 99 | $2023.49

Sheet: Budget Breakdown
Subsystem/Component | Qty. | Unit Cost | Total Cost | Subsystem/Component | Qty. | Unit Cost | Total Cost |  |  | hardware | $160.27 |  | game board | $182.09
Central Controller |  |  |  | Chassis |  |  |  |  | qty | per unit | total | qty | ppu | total
Arduino Mega | 1 | $34.25 | $34.25 | Acrylic | 4 | $19.32 | $77.28 | screws | 1 | $0.99 | $0.99 | 1 | 8.12 | $8.12
 |  | Total | $34.25 |  |  | Total | $77.28 | screws | 1 | $7.58 | $7.58 | 4 | 11.98 | $47.92
Vision System |  |  |  | Turntable |  |  |  | screws | 1 | $10.86 | $10.86 | 1 | 9.87 | $9.87
Raspberry Pi | 1 | $149.99 | $149.99 | Motor Mount | 1 | $19.95 | $19.95 | screws | 1 | $7.88 | $7.88 | 3 | 4.96 | $14.88
Camera | 2 | $29.99 | $59.98 | Motor | 1 | $34.99 | $34.99 | screws | 1 | $20.00 | $20.00 | 1 | 6.98 | $6.98
 |  | Total | $209.97 |  |  | Total | $54.94
Peripherals |  |  |  | Shooting Mechanism |  |  |  | screws | 1 | $1.29 | $1.29 | 1 | 3.98 | $3.98
Arduino Uno | 1 | $20.98 | $20.98 | Belt | 1 | $20.98 | $20.98 | caps | 3 | $0.99 | $2.97 | 1 | 5.1 | $5.10
Screen | 1 | $9.99 | $9.99 | Compartment Motor | 1 | $19.95 | $19.95 | diode | 3 | $1.19 | $3.57 | 2 | 2.62 | $5.24
LEDs | 1 | $7.99 | $7.99 | Coupling | 1 | $4.99 | $4.99 | caps | 6 | $1.79 | $10.74 | 1 | 35 | $35.00
Audio Shield | 1 | $34.95 | $34.95 | Shaft | 1 | $8.02 | $8.02 | caps | 6 | $3.29 | $19.74 | 3 | 15 | $45.00
 |  | Total | $73.91 | Bearings | 3 | $9.56 | $28.68 | bread | 1 | $10.28 | $10.28
Arm |  |  |  | Driver Motor | 1 | $24.95 | $24.95 | wires | 1 | $30.00 | $30.00
Arm | 1 | $399.00 | $399.00 |  |  | Total | $107.57 | adapters | 1 | $5.99 | $5.99
Arm Servo | 1 | $17.50 | $17.50 | Power |  |  |  | flashlights | 4 | $2.00 | $8.00
 |  | Total | $416.50 | Emergency Stop | 1 | $12.99 | $12.99 | screws | 1 | $8.32 | $8.32
Drive Train |  |  |  | Start/Stop Switch | 2 | $14.85 | $29.70 | inserts | 1 | $12.06 | $12.06
Wheels | 1 | $70.94 | $70.94 | Wall Wart | 1 | $16.99 | $16.99
H-Bridge | 2 | $8.99 | $17.98 | Buck | 1 | $15.99 | $15.99
Motor | 5 | $24.95 | $124.75 | Buck Boost | 1 | $55.99 | $55.99
IR Sensors | 4 | $8.99 | $35.96 | Power Bus | 3 | $9.49 | $28.47
Ling Following Sensors | 3 | $7.00 | $21.00 | Battery Charger | 1 | $35.95 | $35.95
 |  | Total | $270.63 | Battery | 2 | $120.00 | $240.00
General |  |  |  |  |  | Total | $436.08
Gameboard supplies |  |  | $182.09 | Grand Total |  |  | $2023.49
Hardware |  |  | $160.27
 |  | Total | $342.36
 |  |  | $0.00
 |  |  | $0.00
 |  |  | $0.00
 |  |  | $0.00
 |  |  | $0.00
 |  |  | $0.00

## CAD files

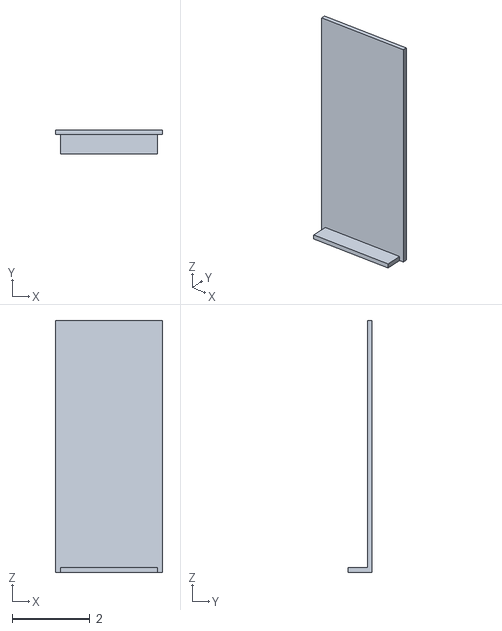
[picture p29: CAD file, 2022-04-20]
Documentation/DesignDocuments/3D Models/False_Bottom_2.obj
2.75 x 0.625 x 6.50

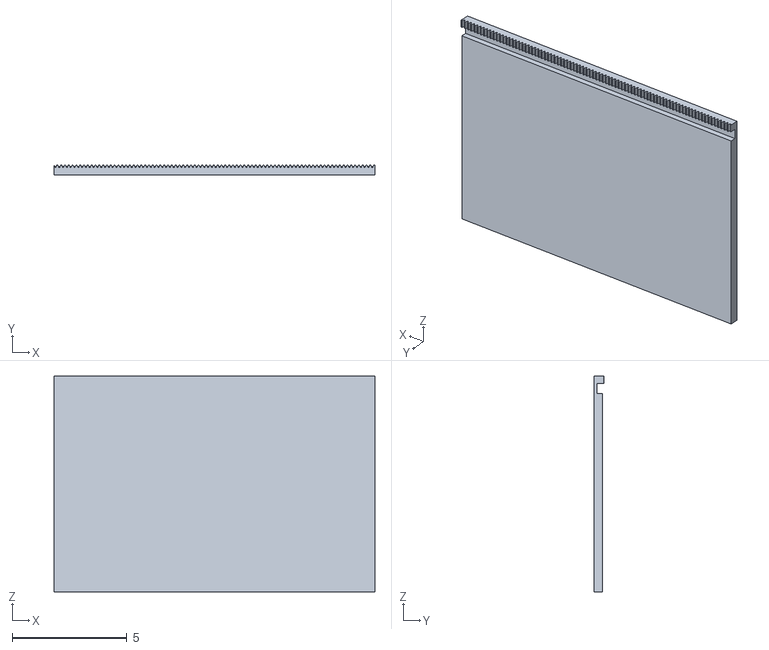
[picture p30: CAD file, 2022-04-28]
Documentation/DesignDocuments/3D Models/STL Files/False_Bottom_Geared_2.stl
14.0 x 0.444 x 9.40

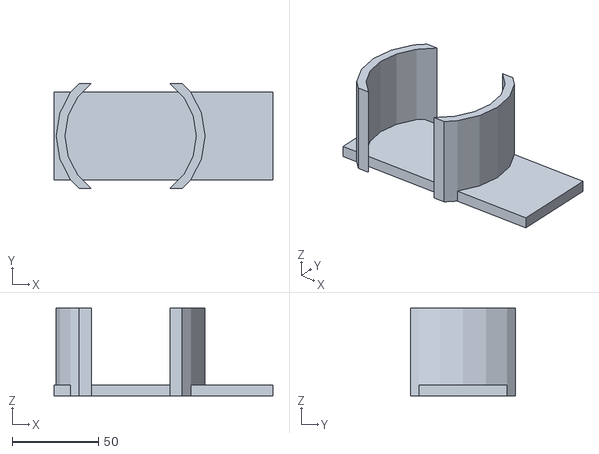
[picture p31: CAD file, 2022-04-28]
Documentation/DesignDocuments/3D Models/STL Files/Final SEC22 Cup Holder.stl
127.0 x 61.0 x 50.8

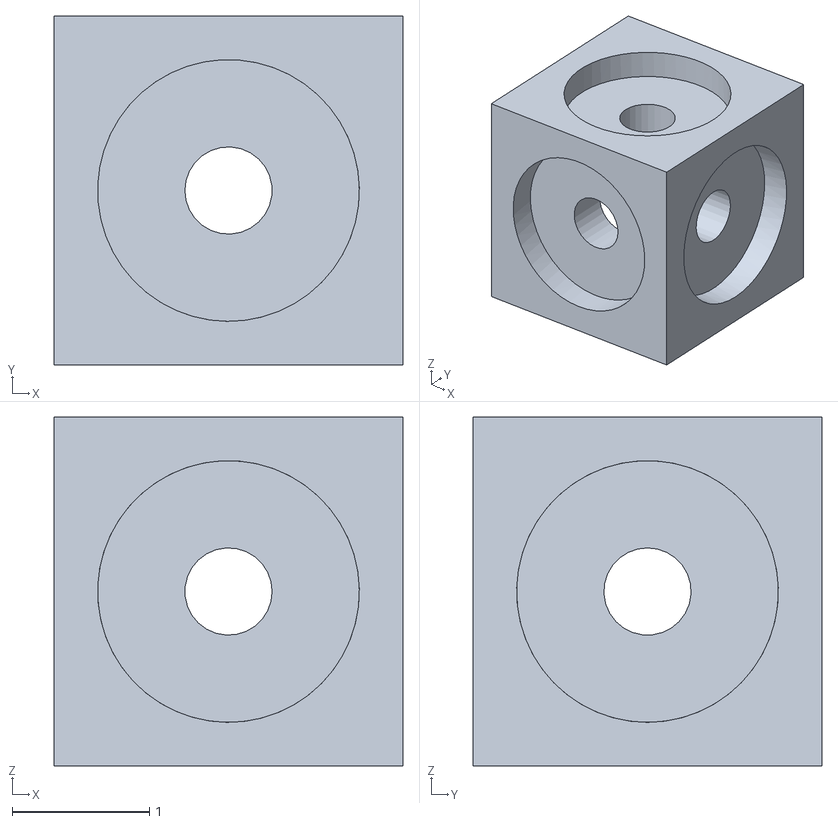
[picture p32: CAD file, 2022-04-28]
Documentation/DesignDocuments/3D Models/STL Files/MountingBracket_2.stl
2.54 x 2.54 x 2.54

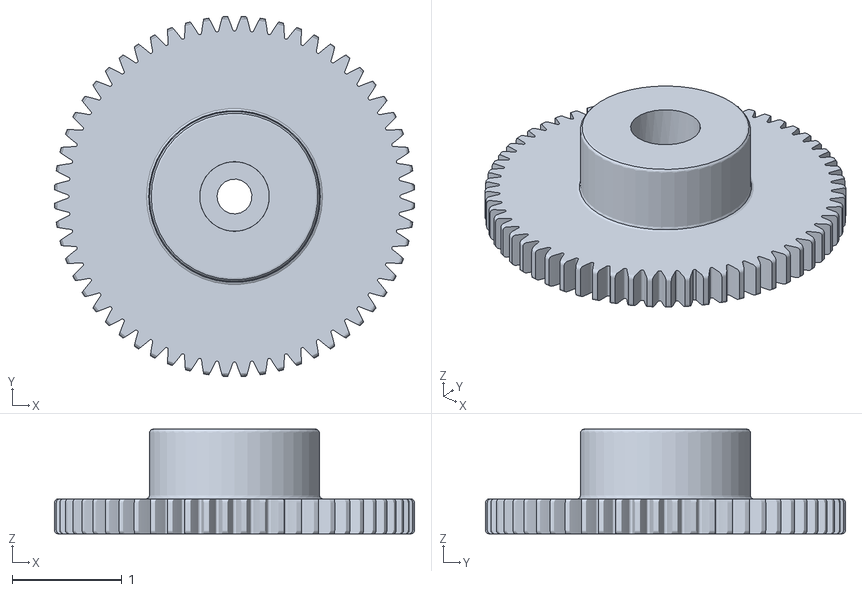
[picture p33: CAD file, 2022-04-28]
Documentation/DesignDocuments/3D Models/STL Files/ShootingMech_ReloadGear.stl
3.27 x 3.27 x 0.952

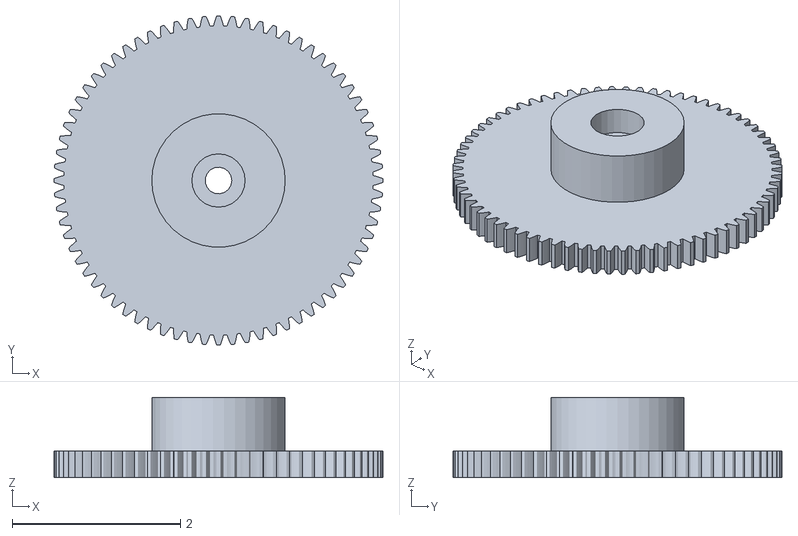
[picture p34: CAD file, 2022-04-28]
Documentation/DesignDocuments/3D Models/STL Files/Spur Gear21.stl
3.92 x 3.92 x 0.952

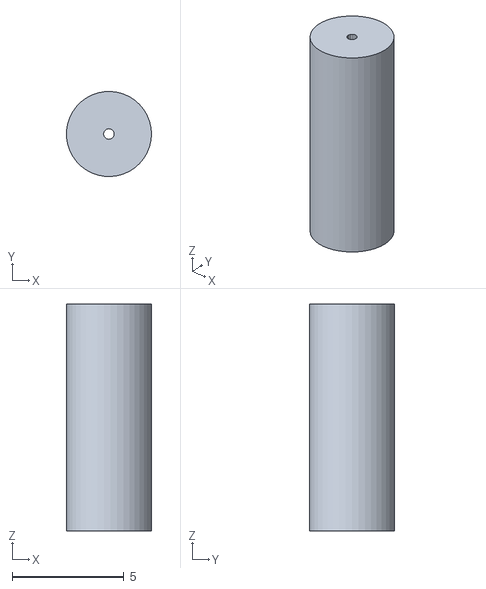
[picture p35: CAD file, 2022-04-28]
Documentation/DesignDocuments/3D Models/STL Files/ShootingMech_Roller.stl
3.80 x 3.81 x 10.2

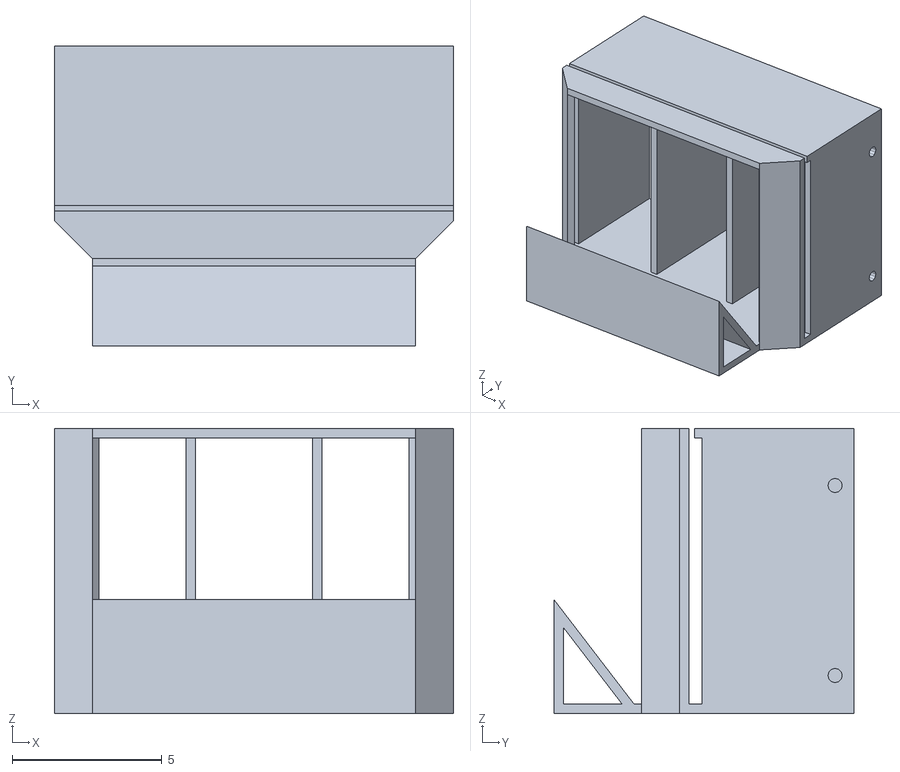
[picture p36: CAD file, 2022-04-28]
Documentation/DesignDocuments/3D Models/STL Files/BeadCompartments_5.stl
13.3 x 10.0 x 9.53

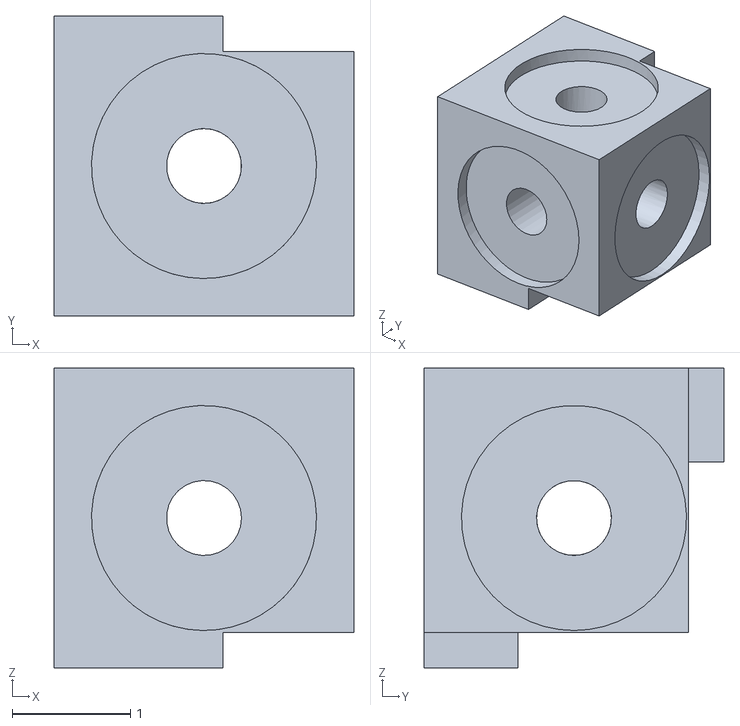
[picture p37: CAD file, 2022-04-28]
Documentation/DesignDocuments/3D Models/STL Files/MountingBracket_4.stl
2.54 x 2.54 x 2.54

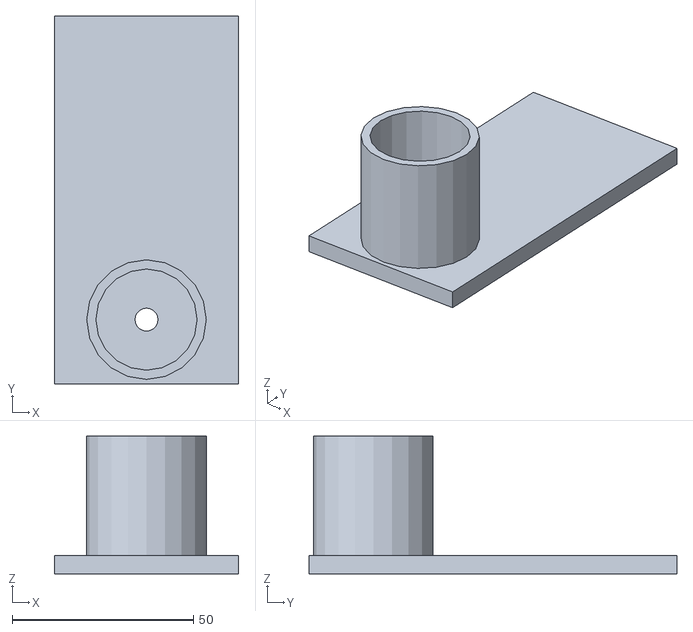
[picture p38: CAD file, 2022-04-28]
Documentation/DesignDocuments/3D Models/STL Files/Net holder_final.stl
50.8 x 101.6 x 38.1

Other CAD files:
Documentation/DesignDocuments/Power/Current Power CAD Packet/000_001.dwg
Documentation/DesignDocuments/Power/Current Power CAD Packet/200_006.dwg
Documentation/DesignDocuments/Power/Current Power CAD Packet/100_416.dwg
Documentation/DesignDocuments/Power/Current Power CAD Packet/100_014.dwg
Documentation/DesignDocuments/Power/Current Power CAD Packet/100_008.dwg
Documentation/DesignDocuments/Power/Current Power CAD Packet/200-002.dwg
Documentation/DesignDocuments/Power/Current Power CAD Packet/200_201.dwg
Documentation/DesignDocuments/Power/Current Power CAD Packet/300_002.dwg
Documentation/DesignDocuments/3D Models/1327K108_Rotary Shaft.SLDPRT
Documentation/DesignDocuments/3D Models/1327K108_Rotary Shaft.ipt
Documentation/DesignDocuments/3D Models/1346K17_Rotary Shaft.ipt
Documentation/DesignDocuments/3D Models/2662N26_20 Degree Pressure Angle Plastic Gear.ipt
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

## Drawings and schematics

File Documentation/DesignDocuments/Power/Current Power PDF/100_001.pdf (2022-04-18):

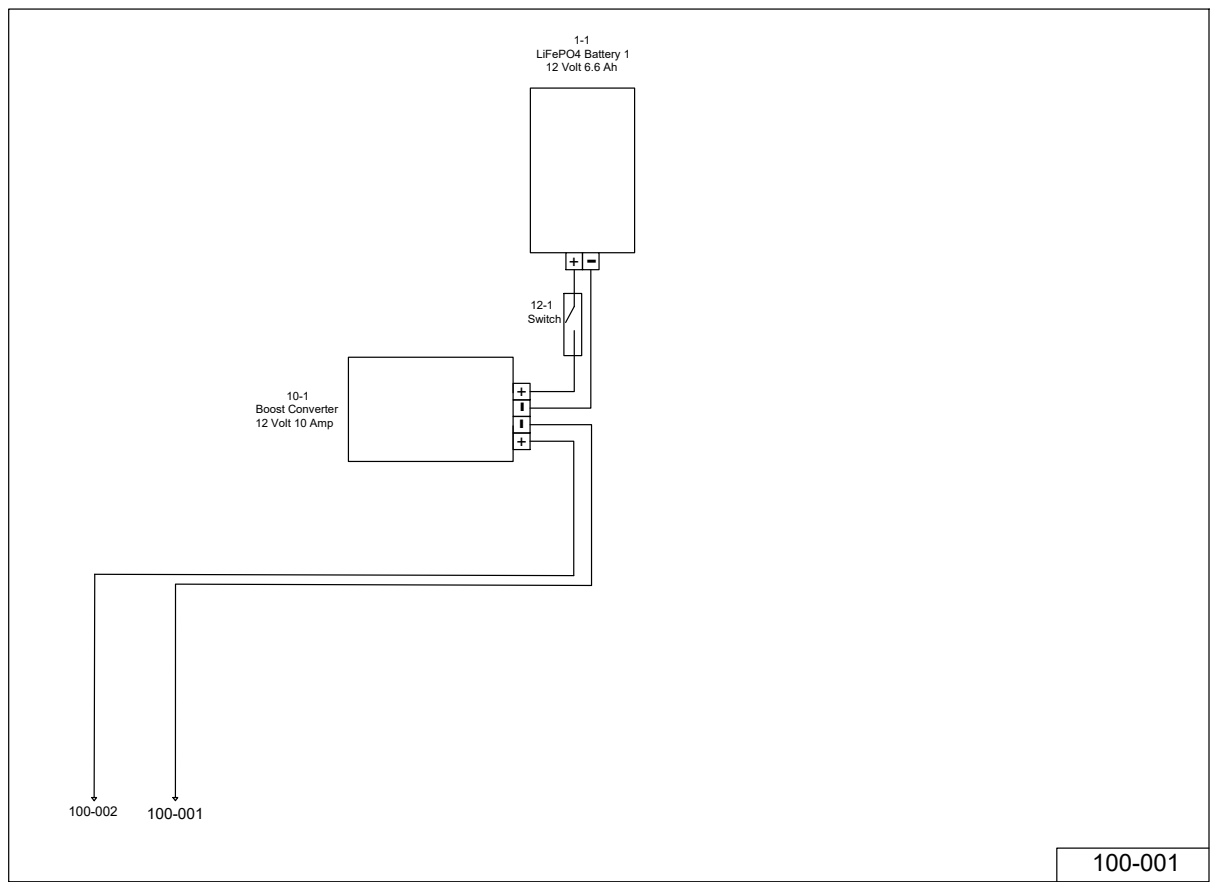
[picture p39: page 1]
LiFePO4 Battery 1 12 Volt 6.6 Ah; Boost Converter 12 Volt 10 Amp

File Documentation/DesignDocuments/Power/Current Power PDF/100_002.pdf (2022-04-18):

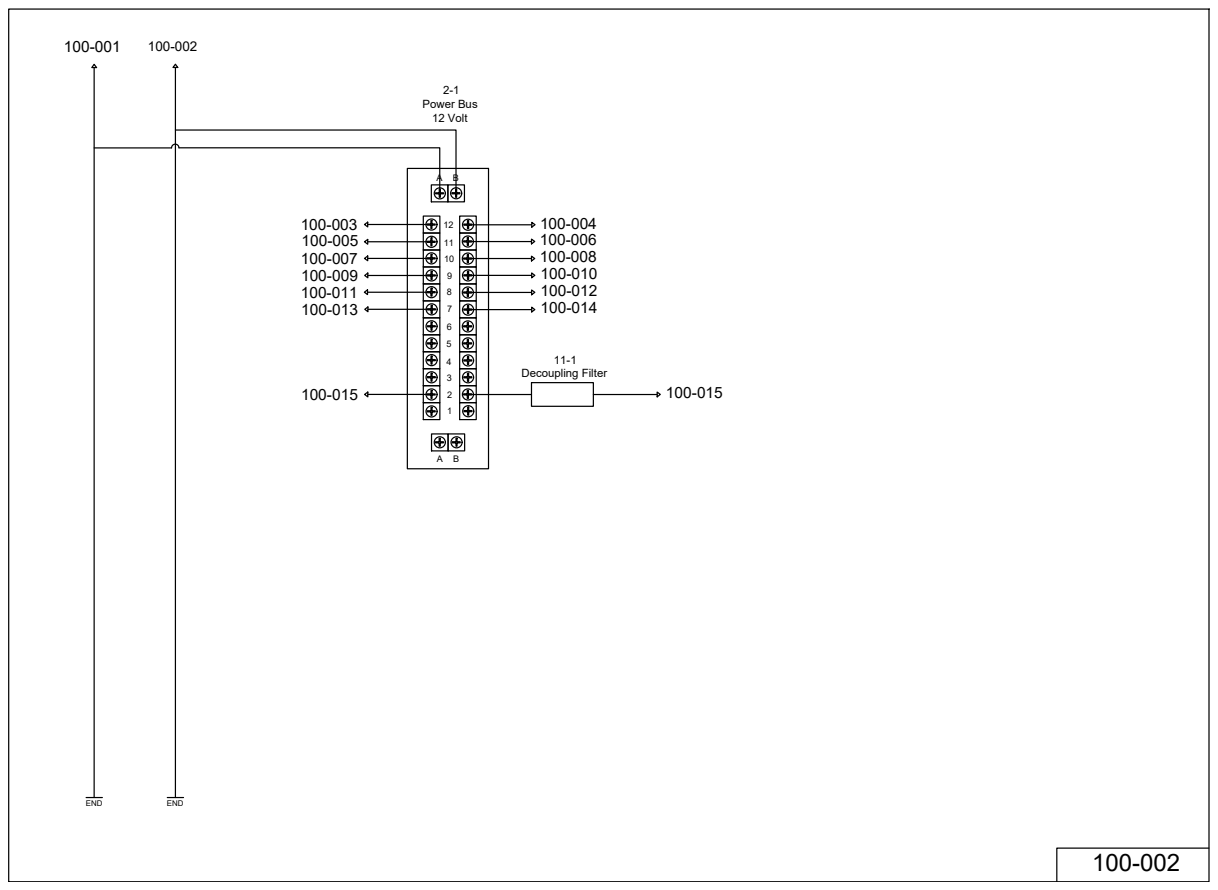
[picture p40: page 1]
Power Bus 12 Volt; Decoupling Filter

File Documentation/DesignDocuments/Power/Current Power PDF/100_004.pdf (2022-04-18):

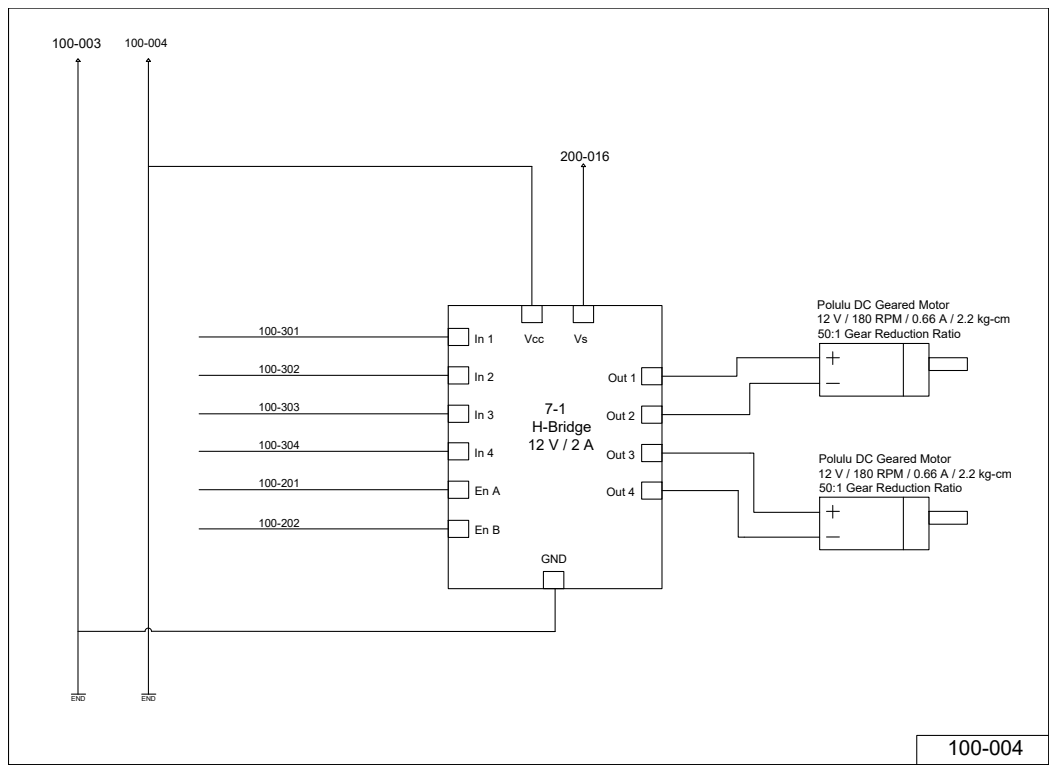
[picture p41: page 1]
Out 1; Out 2; Out 3; Out 4

Polulu DC Geared Motor
12 V / 180 RPM / 0.66 A / 2.2 kg-cm
50:1 Gear Reduction Ratio

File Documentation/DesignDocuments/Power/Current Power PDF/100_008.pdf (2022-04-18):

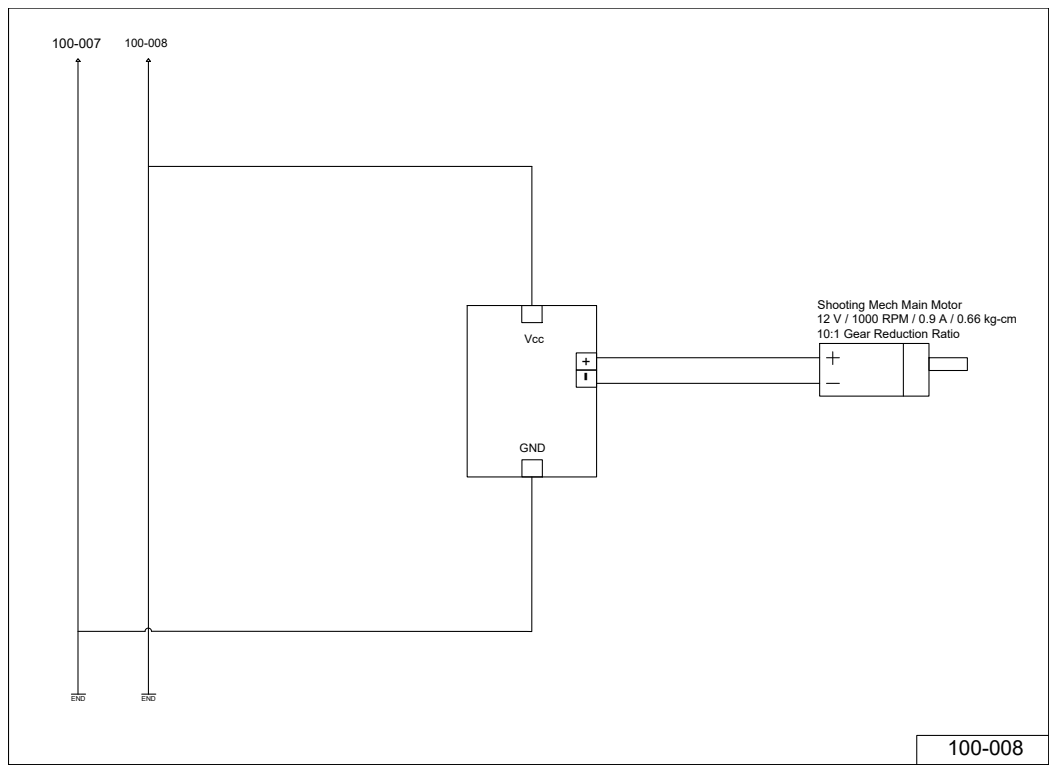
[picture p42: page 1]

Shooting Mech Main Motor
12 V / 1000 RPM / 0.9 A / 0.66 kg-cm

10:1 Gear Reduction Ratio Vcc

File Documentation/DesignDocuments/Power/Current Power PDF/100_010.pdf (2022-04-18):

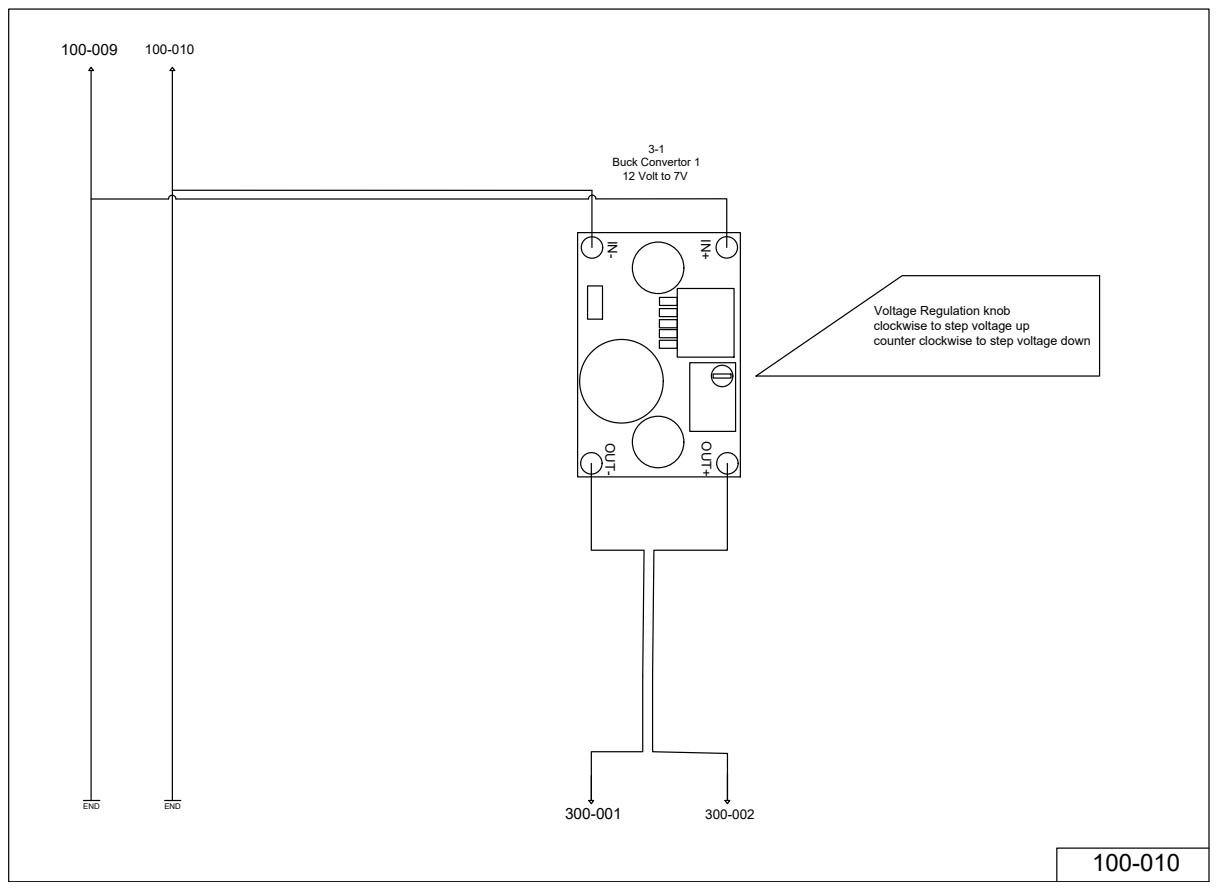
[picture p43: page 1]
END; IN+ OUT-; OUT+; Buck Convertor 1 12 Volt to 7V

Voltage Regulation knob
clockwise to step voltage up
counter clockwise to step voltage down

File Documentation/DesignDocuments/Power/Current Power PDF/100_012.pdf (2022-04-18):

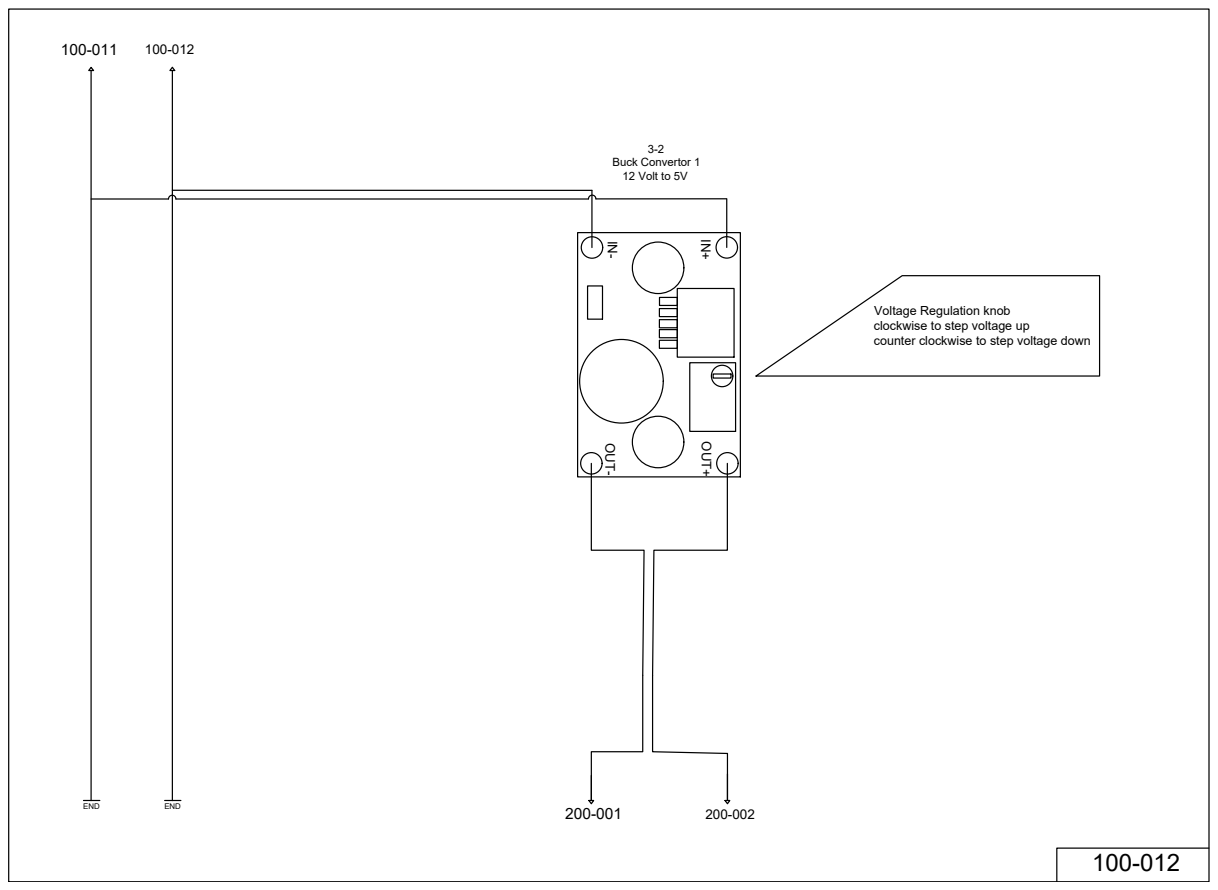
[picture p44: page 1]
END; IN+ OUT-; OUT+; Buck Convertor 1 12 Volt to 5V

Voltage Regulation knob
clockwise to step voltage up
counter clockwise to step voltage down

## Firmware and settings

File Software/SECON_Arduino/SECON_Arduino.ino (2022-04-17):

//WORK ON THE 2ND NET CHECK WHEN TURNING RIGHT


#include <QTRSensors.h>
#include <NewPing.h>
#include <Adafruit_PWMServoDriver.h>
Adafruit_PWMServoDriver pwm = Adafruit_PWMServoDriver();

bool net_positions[7] = {false};

int net_index = 0;
int net_count = 0;
int serial_data = '0';

int check_nets_counter = 0;
int net_shots[7];
int servo_counter = 3;
int shooting_mech_index = 0;




int timer_isr_counter = 0;

#define SERVOMIN  150 // This is the 'minimum' pulse length count (out of 4096)
#define SERVOMAX  600 // This is the 'maximum' pulse length count (out of 4096)
#define USMIN  600 // This is the rounded 'minimum' microsecond length based on the minimum pulse of 150
#define USMAX  2400 // This is the rounded 'maximum' microsecond length based on the maximum pulse of 600
#define SERVO_FREQ 50 // Analog servos run at ~50 Hz updates

#define ftl(x) ((x)>=0?(long)((x)+0.5):(long)((x)-0.5))  //float to long conversion
/* Arm dimensions( mm ) */
#define BASE_HGT 67.31      //base hight 2.65"
#define HUMERUS 146.05      //shoulder-to-elbow "bone" 5.75"
#define ULNA 187.325        //elbow-to-wrist "bone" 7.375"
#define GRIPPER 100.00          //gripper (incl.heavy duty wrist rotate mechanism) length 3.94"

/* Servo names/numbers */
/* Base servo HS-485HB */
#define BAS_SERVO 0
/* Shoulder Servo HS-5745-MG */
#define SHL_SERVO 1
/* Elbow Servo HS-5745-MG */
#define ELB_SERVO 2
/* Wrist servo HS-645MG */
#define WRI_SERVO 8
/* Wrist rotate servo HS-485HB */
#define WRO_SERVO 7
/* Gripper servo HS-422 */
#define GRI_SERVO 5

#define TURNTABLE_SERVO 6 //servo that turns the upper chassis

/* Shooting servo*/
#define SHOOT_SERVO 15


#define SHOOT_EN 17 //enable for relay that drives the shooting motor

float hum_sq = HUMERUS * HUMERUS;
float uln_sq = ULNA * ULNA;

long bas_POS, shl_POS, elb_POS, wri_POS, wro_POS, gri_POS = 0;

//-----------------STATES----------------
bool fwd = true;
bool no_nets = true;
bool rev = false;
bool servos_homed = false;

bool turned_right = false;
bool turned_left = false;


bool net_checks_complete[7] = {false};

void read_distance();

bool return_home = false;

bool first_grab = true;
bool second_grab = false;

bool turning_right = false;
bool turning_left = false;
bool return_nets_3_4 = false;

//---------------------------------------


//-----------DEFINES FOR DRIVETRAIN-------
#define EN_FR 7 //front right motor
#define EN_FL 6 //front left motor
#define EN_RR 5 //rear right motor
#define EN_RL 3 //rear left motor

#define FR_REV 52
#define FR_FWD 53
#define FL_REV 51
#define FL_FWD 50

#define RL_REV 46
#define RL_FWD 47
#define RR_FWD 49
#define RR_REV 48

#define START_SWITCH 4

//#define SHOOTING_EN 17

QTRSensors qtr1; //front sensor
QTRSensors qtr2; //middle sensor
QTRSensors qtr3; //rear sensor

int qtr1_calibMax[8] = {2500};
int qtr1_calibMin[8] = {968, 816, 560, 612, 408, 560, 688, 884};

int qtr2_calibMax[8] = {2500};
int qtr2_calibMin[8] = {736, 1324, 1176, 928, 832, 736, 876, 928};

int qtr3_calibMax[8] = {2500};
int qtr3_calibMin[8] = {652, 652, 508, 552, 604, 552, 604, 1008};

uint16_t position1, position2, position3 = 0; //positions for the 3 line followers

int ignore_count = 0;

/*#define dist_fl 0
#define dist_fr 9
#define dist_rr 3
#define dist_rl 11

float distance_fl, distance_fr, distance_rr, distance_rl = 0.0;*/

NewPing front_sensor(A0, A1, 100); 
NewPing back_sensor(A14, A15, 100);

int distance_front = 0;
int distance_back = 0;


//---------------PID Variables------------------------------
int error, last_error = 0;
int correction = 0;
int p, d, i = 0;
float kp = 0.04;
float ki = 0.0;
float kd = 0.30;
int max_speed = 70;
//--------------------------------------------------------

int motor_speed_fr, motor_speed_fl, motor_speed_rr, motor_speed_rl = 0;

const uint8_t SensorCount = 8;
uint16_t sensorValues[SensorCount];


//----------------FUNCTION PROTOTYPES----------------------
//void motor_fwd();
void robot_fwd();
void motor_stop();
void motors_turn_right();
void motors_turn_left();
void robot_straight_slow();
void run_arm_routine();
void shooting_mech_aim();
void shooting_mech_load();
void crab_walk_right();
void crab_walk_left();
void robot_rev();
void read_distance();
void update_sensors();
void check_nets();
void robot_slow_rev();
void crab_walk_right_turn();
void flick_marshmallow();
void robot_drive_strt_after_turn();
void drive_to_nets_3_4();
void drive_to_nets_5_6();
void drive_to_net_2();
void shoot_nets();
void locate_tree_1();
void locate_tree_2();


//-----------------------------------------------------------

void setup() {
  pinMode(START_SWITCH, INPUT);
  digitalWrite(START_SWITCH, HIGH);

  Serial.begin(9600);
  //Serial.print("Startup");
  //shooting_mech_fire();
  pwm.begin();/*
  In theory the internal oscillator (clock) is 25MHz but it really isn't
  that precise. You can 'calibrate' this by tweaking this number until
  you get the PWM update frequency you're expecting!
  The int.osc. for the PCA9685 chip is a range between about 23-27MHz and
  is used for calculating things like writeMicroseconds()
  Analog servos run at ~50 Hz updates, It is importaint to use an
  oscilloscope in setting the int.osc frequency for the I2C PCA9685 chip.
  1) Attach the oscilloscope to one of the PWM signal pins and ground on
     the I2C PCA9685 chip you are setting the value for.
  2) Adjust setOscillatorFrequency() until the PWM update frequency is the
     expected value (50Hz for most ESCs)
  Setting the value here is specific to each individual I2C PCA9685 chip and
  affects the calculations for the PWM update frequency.
  Failure to correctly set the int.osc value will cause unexpected PWM results
*/
  pwm.setOscillatorFrequency(27000000);
  pwm.setPWMFreq(SERVO_FREQ);  // Analog servos run at ~50 Hz updates
  pwm.setPWM(BAS_SERVO, 0, 410);
  pwm.setPWM(SHL_SERVO, 0, 420);
  pwm.setPWM(ELB_SERVO, 0, 400);
  pwm.setPWM(WRI_SERVO, 0, 100);
  pwm.setPWM(WRO_SERVO, 0, 325);
  pwm.setPWM(GRI_SERVO, 0, 100);
  servos_homed = true;
  //delay(1500);

  pwm.setPWM(TURNTABLE_SERVO, 0, 80);

  //Define motor direction and PWM pins
  pinMode(EN_RR, OUTPUT); //Front Left PWM
  pinMode(EN_RL, OUTPUT); //Front Right PWM
  pinMode(EN_FR, OUTPUT); //Rear Left PWM
  pinMode(EN_FL, OUTPUT); //Rear Right PWM
  pinMode(RR_FWD, OUTPUT);
  pinMode(RR_REV, OUTPUT);
  pinMode(RL_FWD, OUTPUT);
  pinMode(RL_REV, OUTPUT);
  pinMode(FR_FWD, OUTPUT);
  pinMode(FR_REV, OUTPUT);
  pinMode(FL_FWD, OUTPUT);
  pinMode(FL_REV, OUTPUT);
  pinMode(A0, OUTPUT);
  pinMode(A1, INPUT);
  pinMode(A14, OUTPUT);
  pinMode(A15, INPUT);
  pinMode(SHOOT_EN, OUTPUT);
  
//  digitalWrite(SHOOTING_REV, LOW);


  pinMode(SHOOT_EN, OUTPUT);

  //Set up Pololu Sensors with Library Commands
  qtr3.setTypeRC();
  qtr3.setSensorPins((const uint8_t[]) {
    28, 29, 26, 27, 24, 25, 22, 23
  }, SensorCount);//Define which pins are used
  //qtr3.setEmitterPin(34);

  //Set up Pololu Sensors with Library Commands
  qtr2.setTypeRC();
  qtr2.setSensorPins((const uint8_t[]) {
    36, 37, 34, 35, 32, 33, 30, 31
  }, SensorCount);//Define which pins are used
  //qtr2.setEmitterPin(44);

  qtr1.setTypeRC();
  qtr1.setSensorPins((const uint8_t[]) {
    44, 45, 42, 43, 40, 41, 38, 39
  }, SensorCount);//Define which pins are used
  //qtr1.setEmitterPin(23);

  //Calibrate sensors, take 400 readings
  for (uint16_t i = 0; i < 400; i++)
  {
    qtr1.calibrate();
    qtr2.calibrate();
    qtr3.calibrate();
  }
    //AUTOMATICALLY CALIBRATE LINE FOLLOWING SENSORS
  /*for(int i = 0; i < SensorCount; i++) {
    qtr1.calibrationOn.maximum[i] = qtr1_calibMax[i];
    qtr1.calibrationOn.minimum[i] = qtr1_calibMin[i];

    qtr2.calibrationOn.maximum[i] = qtr2_calibMax[i];
    qtr2.calibrationOn.minimum[i] = qtr2_calibMin[i];

    qtr3.calibrationOn.maximum[i] = qtr3_calibMax[i];
    qtr3.calibrationOn.minimum[i] = qtr3_calibMin[i];
  }
  delay(4000);*/

  //Setup TIMER5 overflow interrupts
  noInterrupts();
  TCCR5A = 0;
  TCCR5B = 0;
  TCCR5B |= (1 << CS52) | (1 << CS50);
  OCR5A = 8192;
  TCCR5B |= (1 << WGM52);
  TIMSK5 |= (1 << OCIE5A);
  TCNT5 = 0;
  interrupts();
  //ADMUX = 0b01100000;
  //ADCSRA = 0b10000100;
  

}


void loop() {
  while(digitalRead(START_SWITCH) == 1) {
    net_positions[7] = {false};
    net_index = 0;
    net_count = 0;
    serial_data = '0';

    check_nets_counter = 0;
    net_shots[7];
    servo_counter = 3;
    shooting_mech_index = 0;




    timer_isr_counter = 0;



//-----------------STATES----------------
    fwd = true;
    no_nets = true;
    rev = false;
    servos_homed = false;

    turned_right = false;
    turned_left = false;


    net_checks_complete[7] = {false};

    read_distance();

    return_home = false;

    first_grab = true;
    second_grab = false;

    turning_right = false;
    turning_left = false;
    return_nets_3_4 = false;

    pwm.setPWM(BAS_SERVO, 0, 410);
    pwm.setPWM(SHL_SERVO, 0, 420);
    pwm.setPWM(ELB_SERVO, 0, 400);
    pwm.setPWM(WRI_SERVO, 0, 100);
    pwm.setPWM(WRO_SERVO, 0, 325);
    pwm.setPWM(GRI_SERVO, 0, 100);
    servos_homed = true;
    //delay(1500);

    pwm.setPWM(TURNTABLE_SERVO, 0, 80);

}

  //Serial.println("Start");
update_sensors();

/*update_sensors();
if(turned_right) {
  if(distance_back >= 40) {
    if(2500 < position1 < 5000) {
      if(position2 == 0 || position2 == 7000) {
        ignore_sensor_fwd = false;
      }
    }
  }
}*/


   check_nets(); //Check for net 0
   //Serial.println("Check net 0 done");
   
   net_index++; //ignore net 1

   //Serial.print("Check nets 0 complete");

   locate_tree_1();


   drive_to_net_2(); //contains right turn, line up at net 2
   check_nets(); //check for net 2

  //drive_to_nets_3_4();
  //check_nets(); //check for nets 3
  //check_nets(); //check for net 4
  //flick_marshmallow();
  net_index++;
  net_index++;
  
  flick_marshmallow(); //drive to gap, flick marshmallow off

  locate_tree_2();

  drive_to_nets_5_6();
  check_nets(); //check for net 5
  //check_nets();// check for net 6
  net_index++;
  
  int arm_move_var_1 = 420;
  int arm_move_var_2 = 400;
  
   //Arm move into position for shot
   for (arm_move_var_1 = 420; arm_move_var_1 != 300; arm_move_var_1 = arm_move_var_1 - 5)

  {

    pwm.setPWM(SHL_SERVO, 0, arm_move_var_1);

    delay(10);

    if (arm_move_var_2 != 325)

    {
      pwm.setPWM(ELB_SERVO, 0, arm_move_var_2);

      ;

      delay(10);

      arm_move_var_2 = arm_move_var_2 - 5;

    }

  }
  
  shoot_nets();
          
return_home = true;
while(digitalRead(START_SWITCH == 0)) {
  if(return_home) {
    if(!turned_left) {
      robot_rev();
      update_sensors();
      if(distance_back <= 10) {
        motor_stop();

        turning_left = true;
        motors_turn_left();
        turned_left = true;
        motor_stop();
      }
    }
    if(turned_left) {
      //robot_slow_rev();
      rev = true;
      fwd = false;
      update_sensors();
      while(distance_back >= 8) {
        update_sensors();
        robot_rev();
      }
      motor_stop();
      update_sensors();
          digitalWrite(SHOOT_EN, HIGH);
          delay(1000);
          shooting_mech_index = 3;
          shooting_mech_load();
          delay(3000);
          digitalWrite(SHOOT_EN, LOW);
          
          return_home = false;
    
      }
   }
 }
 delay(500);
}
  

ISR(TIMER5_COMPA_vect) {

  Serial.println("isr");
  timer_isr_counter++;

  /*if(turned_right) {
    ignore_count++;
  }
  
  check_nets_counter++;

  if(turning_right) {
    turn_right_counter++;
  }
  if(turning_left) {
    turn_left_counter++;
  }

  if(turned_right) {

      turn_right_drive_straight_counter++;
    
  }

  if(return_nets_3_4) {
    return_nets_3_4_counter++;
  }*/
}

void drive_to_net_2() {
  update_sensors();
     fwd = true;
     rev = false;
     max_speed = 80;
  while((distance_front >= 12) && !turned_right) {
        update_sensors();
        //Serial.print(distance_front);
        //Serial.println("      ");
     
        robot_fwd();
     }

   robot_straight_slow();



       motor_stop();
       crab_walk_right_turn();
       motor_stop();
       /*fwd = true;
       rev = false;
       crab_walk_right_turn();
       turning_right = true;*/
       turning_right = true;
       motors_turn_right();
       //fwd = true;
       //rev = false;
       //delay(1000);
       turned_right = true;
     

   if(turned_right) {

    max_speed = 70;

    robot_drive_strt_after_turn();
    delay(500);
    


}
}

void locate_tree_1() {
  update_sensors();
  fwd = true;
  rev = false;
  first_grab = true;
  update_sensors();
    while(distance_front >= 28) {
      //Serial.println(distance_front);
      update_sensors();
      robot_fwd();
    }
      motor_stop();
      delay(500);
      update_sensors(); // redundancy
      max_speed = 65;
      if(distance_front > 22) {
        while(distance_front >= 22) {
        //Serial.println(distance_front);
        update_sensors();
        robot_fwd();
        }
      }

      motor_stop();
        
      run_arm_routine();
      first_grab = false;
      second_grab = true;
      
}

void drive_to_nets_3_4() {
  update_sensors();
  fwd = true;
  rev = false;
  while(distance_back <= 55) {
    update_sensors();
    robot_fwd();
  }
  
  motor_stop();
  delay(500);
  
  update_sensors(); // redundancy

  if(distance_back < 60) {
    while(distance_back <= 60) {
    update_sensors();
    robot_fwd();
    }
  }

    motor_stop();
  
}

void locate_tree_2() {
  update_sensors();
  fwd = true;
  rev = false;
    while(distance_front >= 50 || distance_back <= 65) {
     update_sensors();
     robot_fwd();
    }

    motor_stop();
    update_sensors(); // redundancy

    if(distance_front > 50 || distance_back < 65) {
      while(distance_front >= 50 || distance_back <= 65) {
      update_sensors();
      robot_fwd();
      }
    }

      motor_stop();
      run_arm_routine();
    
}

void drive_to_nets_5_6() {
  update_sensors();
  fwd = true;
  rev = false;
  while(distance_front >= 29) {
    update_sensors();
    robot_fwd();
  }
  motor_stop();
  delay(500);

  if(distance_front > 15) {
    update_sensors();
    while(distance_front >= 15) {
      update_sensors();
      robot_fwd();
    }
  }

  motor_stop();
  
}

void flick_marshmallow() {
  update_sensors();
  fwd = true;
  rev = false;
  while(distance_back <= 74) {
    update_sensors();
    robot_fwd();
  }
  
  motor_stop();

  if(distance_back < 74) {
    while(distance_back <= 74) {
      update_sensors();
      robot_fwd();
    }
  }


    motor_stop;
  
  
 //******************************************* Start of Sweep ***********************************
//Serial.println("Move the turntable");
  for(int i = 80; i <= 260; i+=5)
{
 // Serial.print("moving turntable");
  pwm.setPWM(TURNTABLE_SERVO, 0, i);
  //Serial.print("moved turntable");
  delay(70);
  //Serial.print("delayed");
}
//Serial.println("Tried to move turntable");
    //home
  pwm.setPWM(BAS_SERVO, 0, 405);

  pwm.setPWM(SHL_SERVO, 0, 400);

  pwm.setPWM(ELB_SERVO, 0, 390);

  pwm.setPWM(WRI_SERVO, 0, 110);

  pwm.setPWM(WRO_SERVO, 0, 310);

  pwm.setPWM(GRI_SERVO, 0, 100);

  delay(100);



  //pwm.setPWM(TURNTABLE_SERVO, 0, 200);



  delay(100);



int a = 405;

 int b = 400;

 int c = 390;

int  d = 110;

 int e = 310;

 int f = 100;

 int delay_time = 20;
 int delay_time_movement = 100;

   for (b = 400; b != 210; b = b - 5)

  {

    pwm.setPWM(SHL_SERVO, 0, b);

    delay(delay_time);

    if (c != 340)

    {
      pwm.setPWM(ELB_SERVO, 0, c);

      Serial.println(b);

      delay(delay_time);

      c = c - 5;

    }
    if(d != 180)

  {

    pwm.setPWM(WRI_SERVO, 0, d);

    delay(delay_time);

    d = d + 5;

  }
  pwm.setPWM(GRI_SERVO, 0, 300);
  
  }
      for (e = 310; e != 450; e = e + 5)

  {

    pwm.setPWM(WRO_SERVO, 0, e);
    
    delay(delay_time);
    
  }

  //creep down
     for (b = 210; b != 207; b = b - 1)

  {

    pwm.setPWM(SHL_SERVO, 0, b);

    delay(delay_time);
  
  }
  

  for(int i = 260; i >= 150; i-=5)
{
  pwm.setPWM(TURNTABLE_SERVO, 0, i);
  delay(70);
}

 for(e = 450; e != 310; e = e - 5)
 {
    pwm.setPWM(WRO_SERVO, 0, e);
    
    delay(delay_time);
 }

  pwm.setPWM(WRI_SERVO, 0, 280);

  pwm.setPWM(ELB_SERVO, 0, 290);


  delay(500);
  
  //home sequence

  //creep and grip
  for (b = 207; b != 210; b = b + 1)

  {

    pwm.setPWM(SHL_SERVO, 0, b);

    delay(delay_time);
  
  }
  pwm.setPWM(GRI_SERVO, 0, 100);

  for (b = 210; b != 400; b = b + 5)
  {
    pwm.setPWM(SHL_SERVO, 0, b);

    delay(delay_time);

  }

    for(c = 290; c != 390; c = c + 5)
    {
      pwm.setPWM(ELB_SERVO, 0, c);

      Serial.println(b);

      delay(delay_time);

    if(d != 110)
    {

        pwm.setPWM(WRI_SERVO, 0, d);

        delay(delay_time);

        d = d - 5;      
    }

    }

 pwm.setPWM(WRI_SERVO, 0, 180);
 

  delay(100);  

    for(int i = 150; i >= 80; i-=5)
{
  pwm.setPWM(TURNTABLE_SERVO, 0, i);
  delay(70);
}

//**************************************
// second sweep
//**************************************

 for(int i = 80; i <= 260; i+=5)
{
 // Serial.print("moving turntable");
  pwm.setPWM(TURNTABLE_SERVO, 0, i);
  //Serial.print("moved turntable");
  delay(70);
  //Serial.print("delayed");
}
//Serial.println("Tried to move turntable");
    //home
  pwm.setPWM(BAS_SERVO, 0, 405);

  pwm.setPWM(SHL_SERVO, 0, 400);

  pwm.setPWM(ELB_SERVO, 0, 390);

  pwm.setPWM(WRI_SERVO, 0, 110);

  pwm.setPWM(WRO_SERVO, 0, 310);

  pwm.setPWM(GRI_SERVO, 0, 100);

  delay(100);


   for (b = 400; b != 210; b = b - 5)

  {

    pwm.setPWM(SHL_SERVO, 0, b);

    delay(delay_time);

    if (c != 340)

    {
      pwm.setPWM(ELB_SERVO, 0, c);

      Serial.println(b);

      delay(delay_time);

      c = c - 5;

    }
    if(d != 180)

  {

    pwm.setPWM(WRI_SERVO, 0, d);

    delay(delay_time);

    d = d + 5;

  }
  pwm.setPWM(GRI_SERVO, 0, 300);
  
  }
      for (e = 310; e != 450; e = e + 5)

  {

    pwm.setPWM(WRO_SERVO, 0, e);
    
    delay(delay_time);
    
  }

  //creep down
     for (b = 210; b != 207; b = b - 1)

  {

    pwm.setPWM(SHL_SERVO, 0, b);

    delay(delay_time);
  
  }
  

  for(int i = 260; i >= 150; i-=5)
{
  pwm.setPWM(TURNTABLE_SERVO, 0, i);
  delay(70);
}

 for(e = 450; e != 310; e = e - 5)
 {
    pwm.setPWM(WRO_SERVO, 0, e);
    
    delay(delay_time);
 }

  pwm.setPWM(WRI_SERVO, 0, 280);

  pwm.setPWM(ELB_SERVO, 0, 290);


  delay(500);
  
  //home sequence

  //creep and grip
  for (b = 207; b != 210; b = b + 1)

  {

    pwm.setPWM(SHL_SERVO, 0, b);

    delay(delay_time);
  
  }
  pwm.setPWM(GRI_SERVO, 0, 100);

  for (b = 210; b != 400; b = b + 5)
  {
    pwm.setPWM(SHL_SERVO, 0, b);

    delay(delay_time);

  }

    for(c = 290; c != 390; c = c + 5)
    {
      pwm.setPWM(ELB_SERVO, 0, c);

      Serial.println(b);

      delay(delay_time);

    if(d != 110)
    {

        pwm.setPWM(WRI_SERVO, 0, d);

        delay(delay_time);

        d = d - 5;      
    }

    }

 pwm.setPWM(WRI_SERVO, 0, 180);
 

  delay(100);  

    for(int i = 150; i >= 80; i-=5)
{
  pwm.setPWM(TURNTABLE_SERVO, 0, i);
  delay(70);
}

  //****************************************************************************************************************************************
  //----------------------------------------------------------------------------------------------------------------------------------------
  //------------------------------------------------- END MARSH CODE -----------------------------------------------------------------------
  //----------------------------------------------------------------------------------------------------------------------------------------
  //****************************************************************************************************************************************
  
}
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

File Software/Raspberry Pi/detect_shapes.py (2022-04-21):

from shapedetector import ShapeDetector
from colorlabeler import ColorLabeler
from shapeLength import ShapeLength
import imutils
import cv2
import serial
import digitalio
import board
from PIL import Image, ImageDraw, ImageFont
from adafruit_rgb_display import ili9341
from adafruit_rgb_display import st7789  # pylint: disable=unused-import
from adafruit_rgb_display import hx8357  # pylint: disable=unused-import
from adafruit_rgb_display import st7735  # pylint: disable=unused-import
from adafruit_rgb_display import ssd1351  # pylint: disable=unused-import
from adafruit_rgb_display import ssd1331  # pylint: disable=unused-import

# First define some constants to allow easy resizing of shapes.
BORDER = 20
FONTSIZE = 48

# Configuration for CS and DC pins (these are PiTFT defaults):
cs_pin = digitalio.DigitalInOut(board.CE0)
dc_pin = digitalio.DigitalInOut(board.D25)
reset_pin = digitalio.DigitalInOut(board.D24)

# Config for display baudrate (default max is 24mhz):
BAUDRATE = 24000000

# Setup SPI bus using hardware SPI:
spi = board.SPI()

disp = st7735.ST7735R(spi, rotation=90,
    cs=cs_pin,
    dc=dc_pin,
    rst=reset_pin,
    baudrate=BAUDRATE,
)


# Create blank image for drawing.
# Make sure to create image with mode 'RGB' for full color.
if disp.rotation % 180 == 90:
    height = disp.width  # we swap height/width to rotate it to landscape!
    width = disp.height
else:
    width = disp.width  # we swap height/width to rotate it to landscape!
    height = disp.height
image = Image.new("RGB", (width, height))

# Get drawing object to draw on image.
draw = ImageDraw.Draw(image)

# Draw a black filled box to clear the image.
draw.rectangle((0, 0, width, height), outline=0, fill=(0, 0, 0))
disp.image(image)

image = Image.open("/home/ttu-secon/Desktop/Vision/tech.bmp")

# Scale the image to the smaller screen dimension
image_ratio = image.width / image.height
screen_ratio = width / height
if screen_ratio < image_ratio:
    scaled_width = image.width * height // image.height
    scaled_height = height
else:
    scaled_width = width
    scaled_height = image.height * width // image.width
image = image.resize((scaled_width, scaled_height), Image.BICUBIC)

# Crop and center the image
x = scaled_width // 2 - width // 2
y = scaled_height // 2 - height // 2
image = image.crop((x, y, x + width, y + height))

# Load a TTF Font
font = ImageFont.truetype("/usr/share/fonts/truetype/dejavu/DejaVuSans.ttf", FONTSIZE)

# Draw Some Text

# Get drawing object to draw on image.
draw = ImageDraw.Draw(image)

text1 = "Happy"
(font_width, font_height) = font.getsize(text1)
draw.text(
    (width // 2 - font_width // 2, (height // 2 - font_height // 2) - (height//3)),
    text1,
    font=font,
    fill=(255, 221, 0),
)
text2 = "Mardi"
(font_width, font_height) = font.getsize(text2)
draw.text(
    (width // 2 - font_width // 2, height // 2 - font_height // 2),
    text2,
    font=font,
    fill=(255, 221, 0),
)
text3 = "Gras!"
(font_width, font_height) = font.getsize(text3)
draw.text(
    (width // 2 - font_width // 2, (height // 2 - font_height // 2) + (height//3)),
    text3,
    font=font,
    fill=(255, 221, 0),
)


# Display image.
disp.image(image)


# init video; USB cams on ports 0 and 2
video_capture_0 = cv2.VideoCapture(0)
video_capture_1 = cv2.VideoCapture(2)

ser = serial.Serial(port='/dev/serial0', baudrate=9600,parity=serial.PARITY_NONE, stopbits=serial.STOPBITS_ONE, bytesize=serial.EIGHTBITS, timeout=1)
ser.reset_input_buffer()
alreadyWritten0 = False
ser.write(b"Hello from Pi!\n")
#ser.close()
#print(ser.readline())

#load the image, convert it to grayscale, blur it slightly, and threshold it
while True:
    # init cameras
    ret0, frame0 = video_capture_0.read()
    ret1, frame1 = video_capture_1.read()
    frame0Contour = frame0.copy()
    frame1Contour = frame1.copy()
    cropped0 = frame0[0:300, 0:1000]
    cropped1 = frame1[0:300, 0:1000]
    resized0 = imutils.resize(cropped0, width=300)
    ratio0 = cropped0.shape[0] / float(resized0.shape[0])
    resized1 = imutils.resize(cropped1, width=300)
    ratio1 = cropped1.shape[0] / float(resized1.shape[0])


    blurred0 = cv2.GaussianBlur(resized0, (5,5), 0)
    gray0 = cv2.cvtColor(blurred0, cv2.COLOR_BGR2GRAY)
    lab0 = cv2.cvtColor(blurred0, cv2.COLOR_BGR2LAB)
    #elimWhite0 = cv2.threshold(gray0, 225, 255, cv2.THRESH_TOZERO_INV)[1]
    #elimDark0 = cv2.threshold(elimWhite0, 80, 255, cv2.THRESH_TOZERO)[1]
    thresh0 = cv2.threshold(gray0, 150, 255, cv2.THRESH_BINARY)[1]


    blurred1 = cv2.GaussianBlur(resized1, (5,5), 0)
    gray1 = cv2.cvtColor(blurred1, cv2.COLOR_BGR2GRAY)
    lab1 = cv2.cvtColor(blurred1, cv2.COLOR_BGR2LAB)
    #elimWhite1 = cv2.threshold(gray1, 225, 255, cv2.THRESH_TOZERO_INV)[1]
    #elimDark1 = cv2.threshold(elimWhite1, 80, 255, cv2.THRESH_TOZERO)[1]
    thresh1 = cv2.threshold(gray1, 150, 255, cv2.THRESH_BINARY)[1]

    cnts0 = cv2.findContours(thresh0.copy(), cv2.RETR_EXTERNAL, cv2.CHAIN_APPROX_SIMPLE)
    cnts0 = imutils.grab_contours(cnts0)

    cnts1 = cv2.findContours(thresh1.copy(), cv2.RETR_EXTERNAL, cv2.CHAIN_APPROX_SIMPLE)
    cnts1 = imutils.grab_contours(cnts1)

    sd = ShapeDetector()
    cl = ColorLabeler()
    sl = ShapeLength()
    numCircles0 = 0

    for c in cnts0:
        #compute the center of the contour
        area = cv2.contourArea(c)
        '''M=cv2.moments(c)
        if M["m00"] != 0:
            cX = int(M["m10"] / (M["m00"])) + 250
            cY = int(M["m01"] / (M["m00"]))
        else:
            cX = int(M["m10"] / (M["m00"] + 1))
            cY = int(M["m01"] / (M["m00"] + 1))'''
        shape = sd.detect(c)
        color = cl.label(lab0, c)
        length = sl.detect(c)
        #text = "{} {} {} {}".format(area, color,shape,length)
        

        '''c = c.astype(float)
        c *= ratio0
        c = c.astype(int)'''

        if area > 3000 and area < 5000 and color == "white" and shape == "circle":
            #draw the contour an dcenter of the shape on the image
            numCircles0 = numCircles0 + 1
            '''cv2.drawContours(cropped0, [c], -1, (0,255, 0), 2)
            cv2.circle(cropped0, (cX, cY), 7, (255,255,255), -1)
            cv2.putText(cropped0, text, (cX - 20, cY - 20), cv2.FONT_HERSHEY_SIMPLEX, 0.5, (255,255,255), 2)'''
            #ser.write(b'X')
            #print('X')

    #if numCircles0 == 0:
    #   ser.write(b'A')
    #    print('A')
        
    numCircles1 = 0

    for c in cnts1:
        #compute the center of the contour
        area = cv2.contourArea(c)
        
        '''M=cv2.moments(c)
        if M["m00"] != 0:
            cX = int(M["m10"] / (M["m00"])) + 250
            cY = int(M["m01"] / (M["m00"]))
        else:
            cX = int(M["m10"] / (M["m00"] + 1))
            cY = int(M["m01"] / (M["m00"] + 1))'''
        shape = sd.detect(c)
        color = cl.label(lab1, c)
        length = sl.detect(c)
        #text = "{} {} {} {}".format(area, color,shape,length)
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

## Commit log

2022-04-17 Repo Setup - Adding Documentation
    Initial Setup of Repository. Added Project Documentation and Arduino Files
2022-04-17 Repo Setup - Added Design Documents for Power
    Initial Upload of Power Documents to DesignDocuments folder
    [000_001.dwg, 000_002.dwg, 100_001.dwg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]
2022-04-17 Delete Final Power Packet directory
    Moved to Documentation/DesignDocuments/Power
    [000_001.dwg, 000_002.dwg, 100_001.dwg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]
2022-04-20 Repo Setup - Added 3D Models
    Updated the documentation folder to include all necessary Autodesk Inventor files to construct the robot.
    [1327K108_Rotary Shaft.0001.ipt, 1327K108_Rotary Shaft.0002.ipt, 1327K108_Rotary Shaft.SLDPRT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]
2022-04-21 Repo Setup - Added Raspberry Pi Software Files
    Added Raspberry Pi files and README detailing the Pi software
    [SECON_2022_MasterBOM.xlsx]
2022-04-28 Added STL Files
    Added STL Files for web browser viewing of 3D models
    [BeadCompartments_5.stl, False_Bottom_Geared_2.stl, Final SEC22 Cup Holder.stl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]
2022-04-29 Added BOM
    [SECON_2022_MasterBOM.xlsx]
2022-04-29 Added BOM Again
    [SECON2022_MasterBOM.xlsx]
